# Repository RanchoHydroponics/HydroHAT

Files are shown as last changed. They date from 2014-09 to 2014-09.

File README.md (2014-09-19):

HydroHAT
========

The HydroHAT is an Arduino-based extension to the RPi Model B+. It controls sensors and actuators over I2C and takes care of control loops and lower-level logic, while using the RPi to run the user interface, via a touchscreen and a web interface.

In our case, it is being developed and used to control a hydroponics system, however, it should function well as a general controller for automation via RPi.

Additionally, the UART TX and RX from the RPi are passed through to a 4D Systems header for use with a 4D Systems touchscreen.

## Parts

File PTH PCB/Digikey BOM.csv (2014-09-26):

Digikey PN | Qty
478-5741-ND | 4
ATMEGA1284P-PU-ND | 1
768-1007-1-ND | 1
CAT24C32LI-G-ND | 1
952-1767-ND | 1
952-2219-ND | 1
A19470-ND | 2
609-3221-ND | 1
A19471-ND | 1
A1922-ND | 1
CF14JT10K0CT-ND | 1
490-1215-ND | 1
450-1650-ND | 1
296-16843-1-ND | 3

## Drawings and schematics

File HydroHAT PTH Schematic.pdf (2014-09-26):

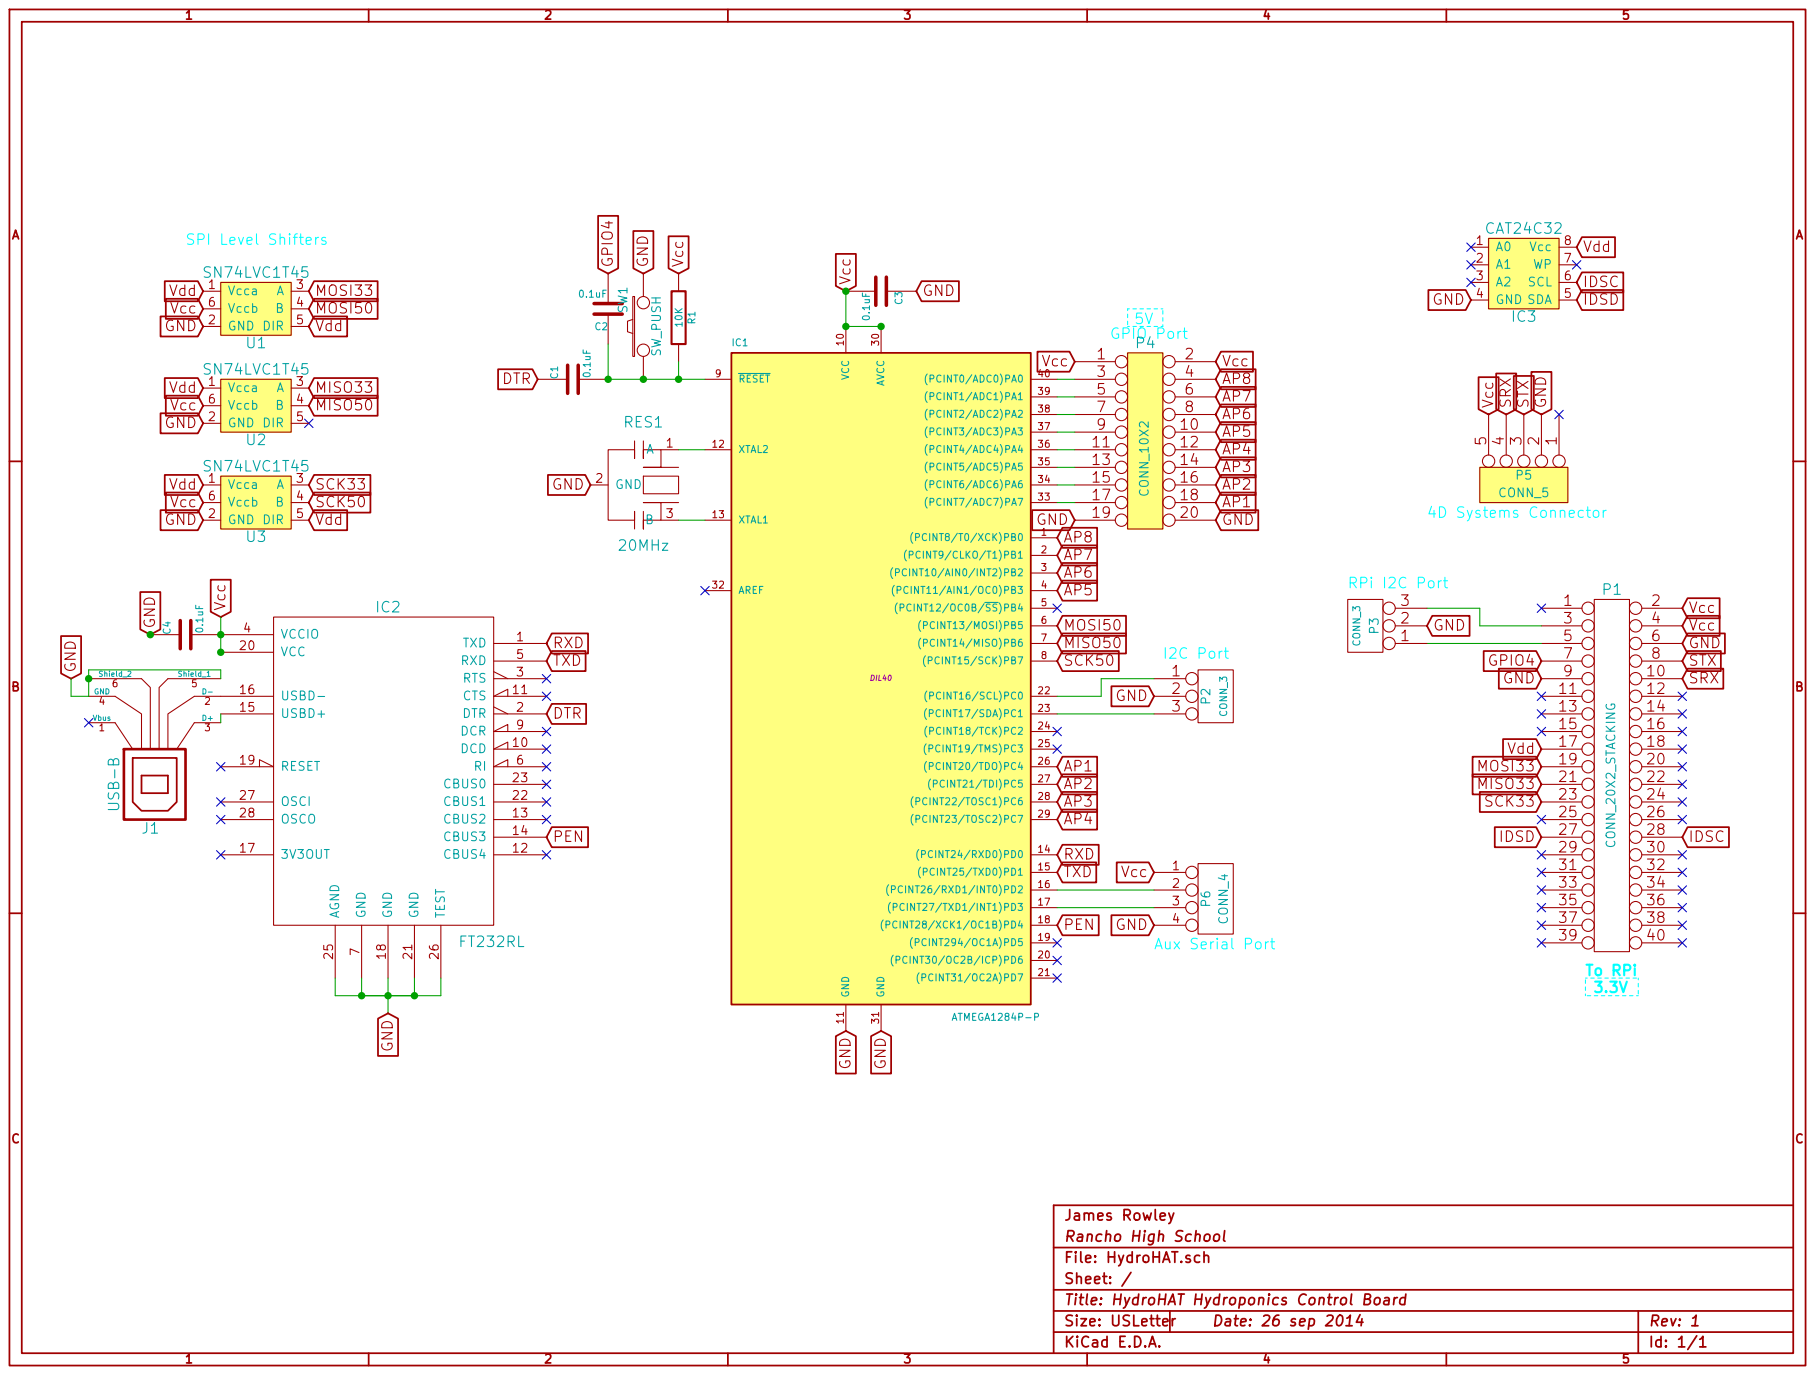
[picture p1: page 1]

SCK50 Vdd Vdd Vdd Vdd Vcc Vcc Vcc GND

P5 CONN_5 Vcc SRX STX GND

7 DCR 9 DCD 10 VCC 20 CTS 11 GND 21 CBUS4 12 CBUS1 22 CBUS2 13 CBUS0 23 CBUS3 14 USBD+ 15 AGND 25 USBD- 16 TEST 26

James Rowley
Rancho High School
File: HydroHAT.sch
Sheet: /
Title: HydroHAT Hydroponics Control Board
KiCad E.D.A.

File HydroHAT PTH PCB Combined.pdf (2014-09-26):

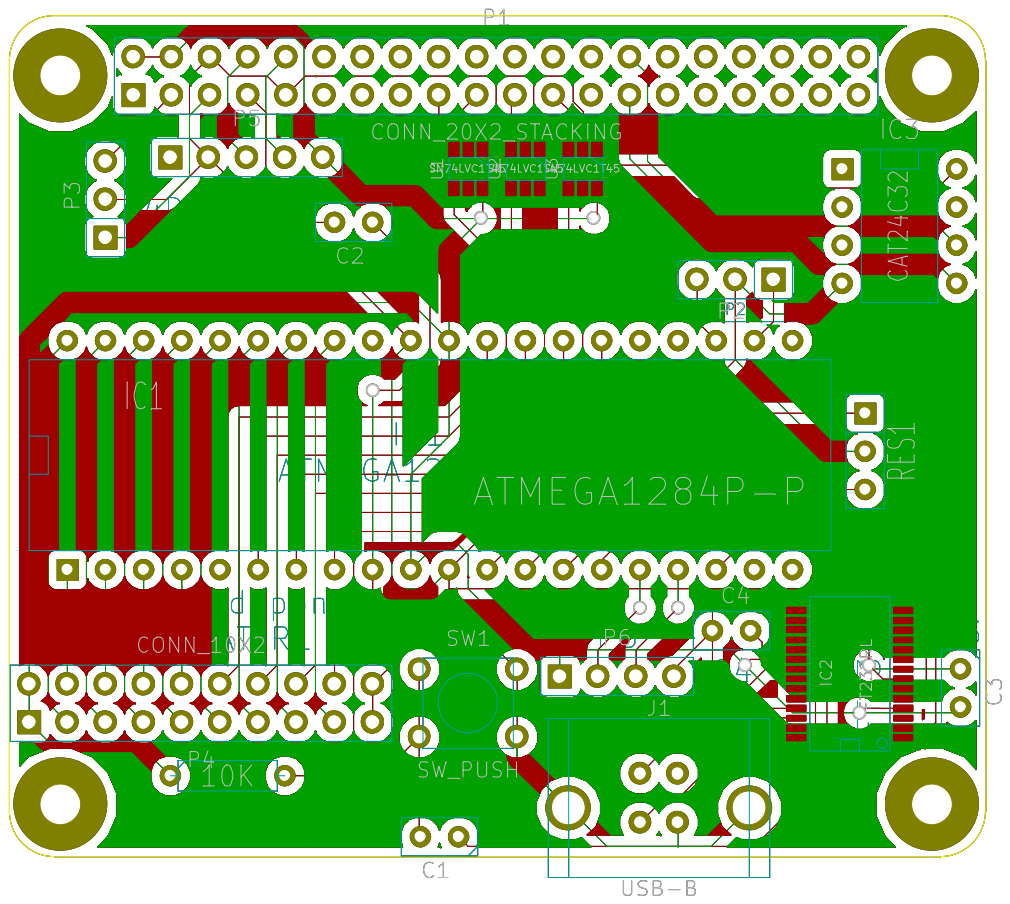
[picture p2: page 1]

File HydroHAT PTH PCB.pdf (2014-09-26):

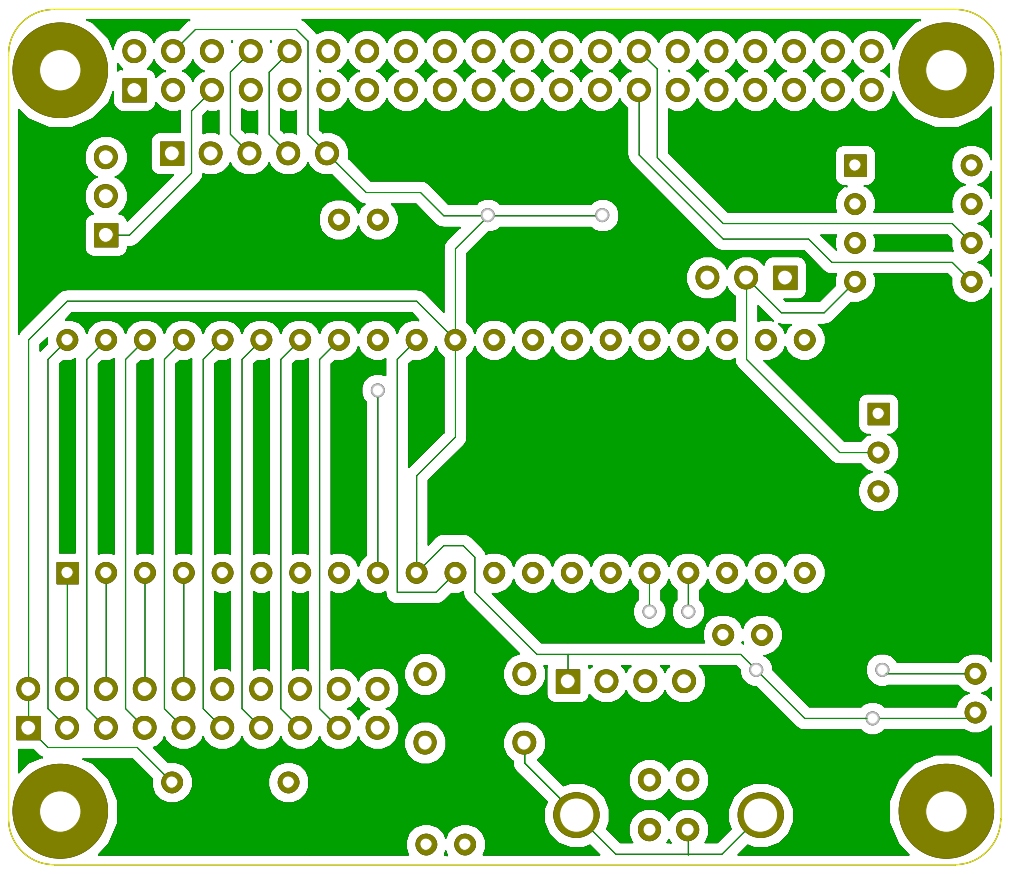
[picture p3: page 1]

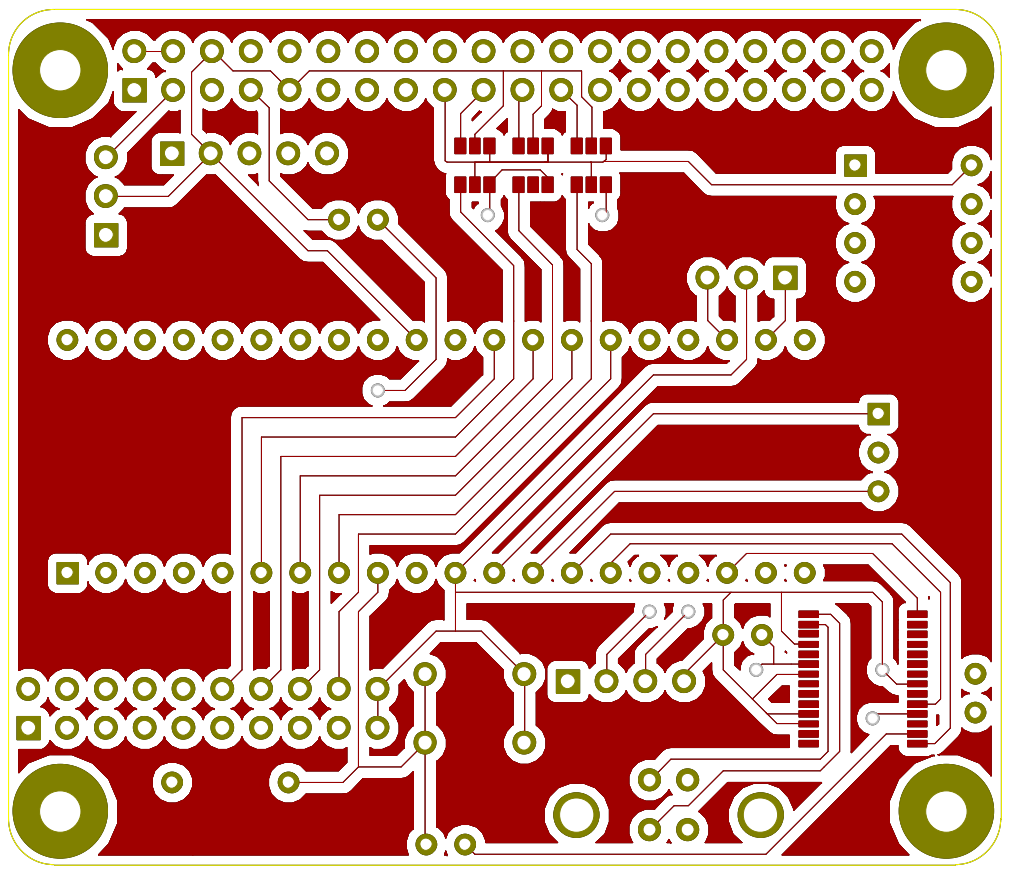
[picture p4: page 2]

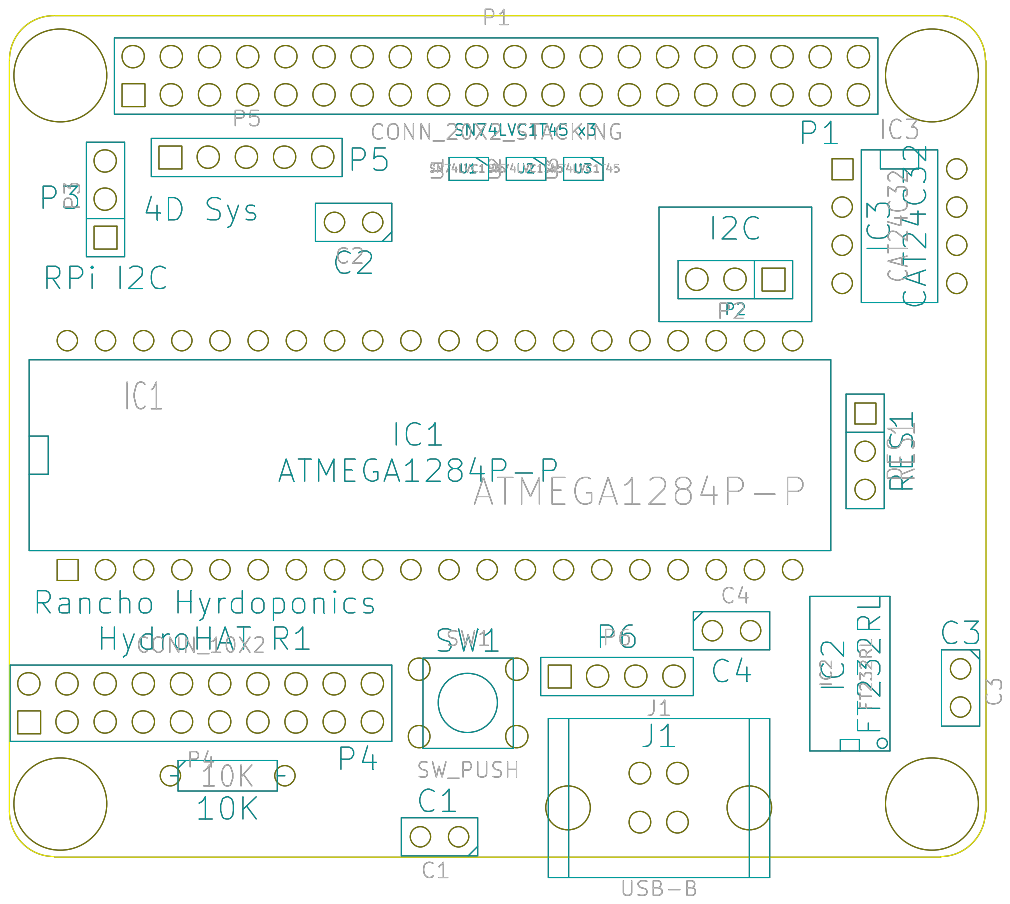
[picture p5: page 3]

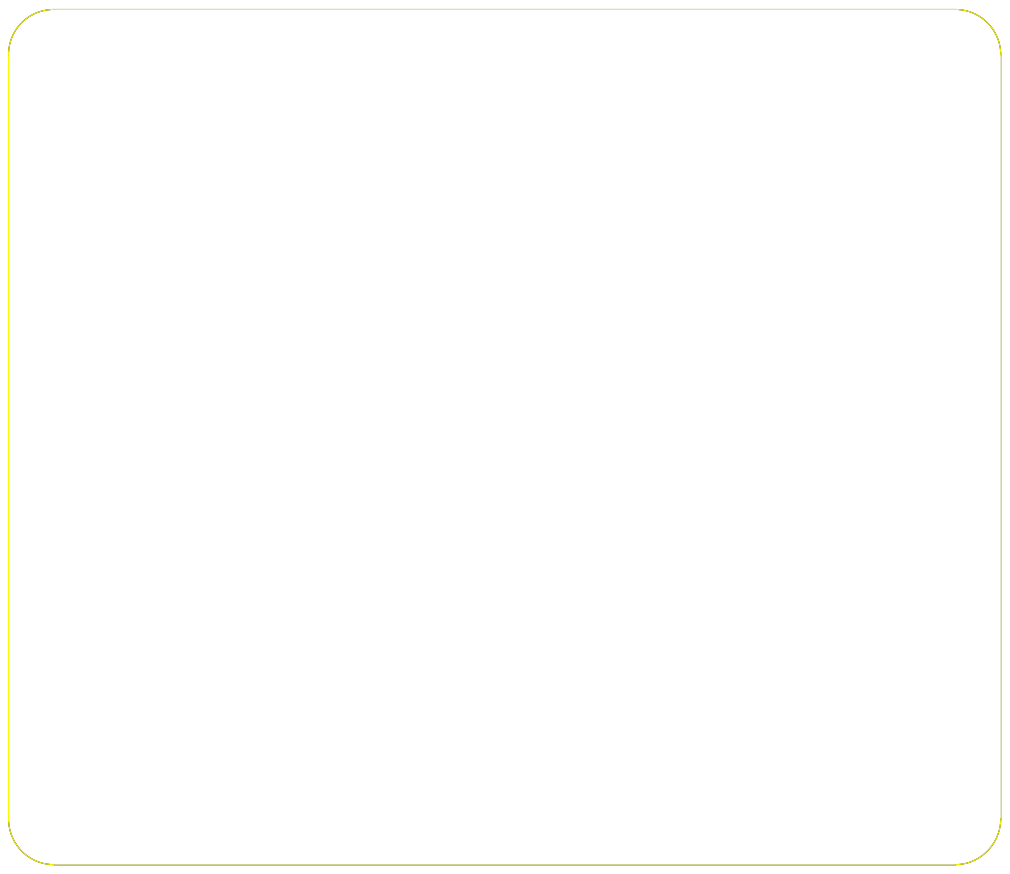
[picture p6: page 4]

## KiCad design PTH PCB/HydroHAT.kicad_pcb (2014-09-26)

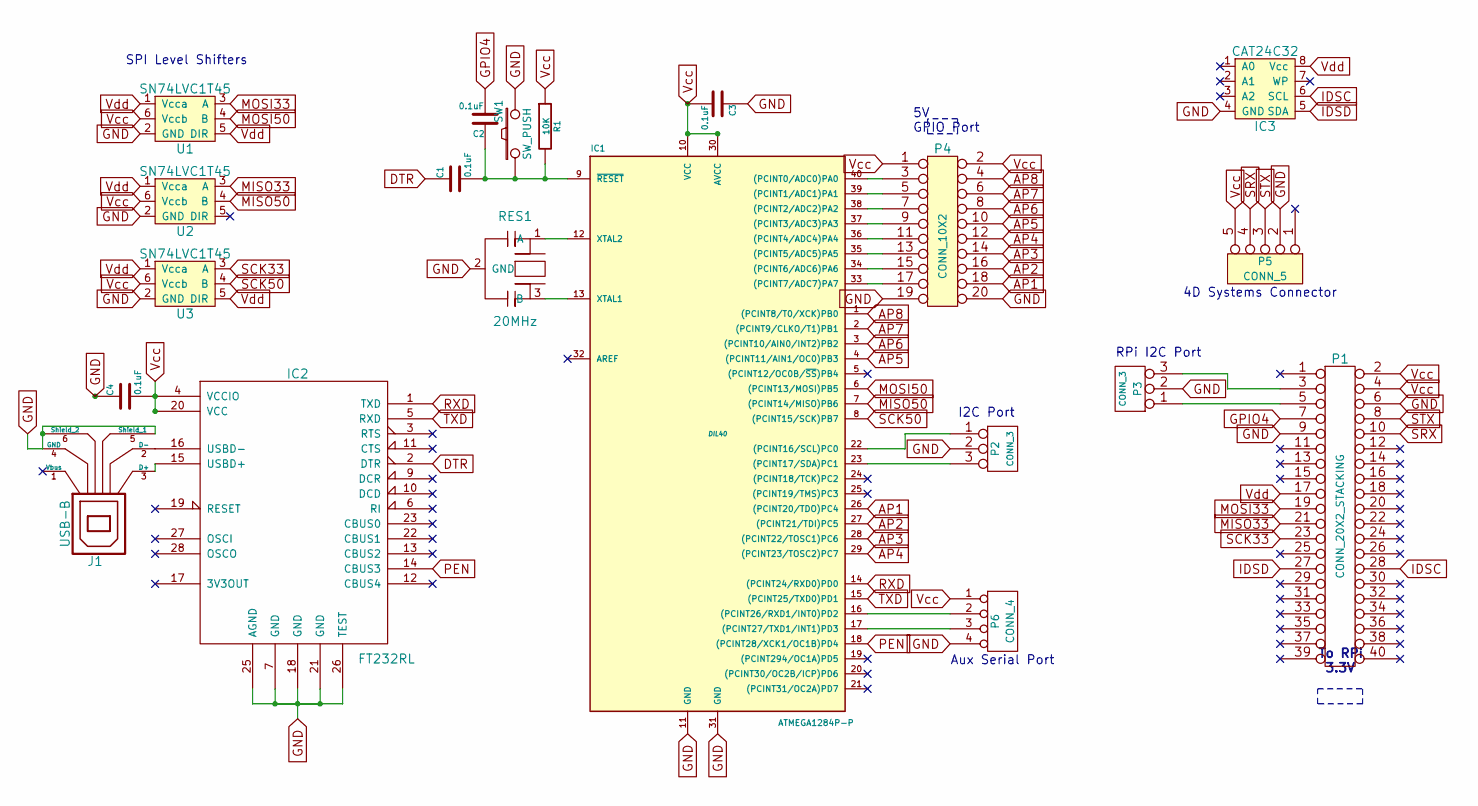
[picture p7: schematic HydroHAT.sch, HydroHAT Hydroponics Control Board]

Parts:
C1, C2, C3, C4: 0.1uF; MFG Part Num SR295E104MAR
IC1: ATMEGA1284P-P; DIL40; MFG Part Num ATMEGA1284P-PU
IC2: FT232RL; MFG Part Num FT232RL-TUBE
IC3: CAT24C32; MFG Part Num CAT24C32LI-G
J1: USB-B; MFG Part Num M701-330442
P1: CONN_20X2_STACKING; MFG Part Num M20-6102045
P2, P3: CONN_3; MFG Part Num 640456-3
P4: CONN_10X2; MFG Part Num 67996-420HLF
P5: CONN_5; MFG Part Num 640456-5
P6: CONN_4; MFG Part Num 640456-4
R1: 10K; MFG Part Num CF14JT10K0
RES1: 20MHz; MFG Part Num CSTLS20M0X53-B0
SW1: SW_PUSH; MFG Part Num 1825910-6
U1, U2, U3: SN74LVC1T45; MFG Part Num SN74LVC1T45DBVR

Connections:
AP1: IC1.26 ((PCINT20/TDO)PC4), P4.18
AP2: IC1.27 ((PCINT21/TDI)PC5), P4.16
AP3: IC1.28 ((PCINT22/TOSC1)PC6), P4.14
AP4: IC1.29 ((PCINT23/TOSC2)PC7), P4.12
AP5: IC1.4 ((PCINT11/AIN1/OC0)PB3), P4.10
AP6: IC1.3 ((PCINT10/AIN0/INT2)PB2), P4.8
AP7: IC1.2 ((PCINT9/CLKO/T1)PB1), P4.6
AP8: IC1.1 ((PCINT8/T0/XCK)PB0), P4.4
DTR: C1.1, IC2.2 (DTR)
GND: C3.1, C4.1, IC1.11 (GND), IC1.31 (GND), IC2.7 (GND), IC2.18 (GND), IC2.21 (GND), IC2.25 (AGND), IC2.26 (TEST), IC3.4 (GND), J1.4 (GND), J1.5 (Shield_1), J1.6 (Shield_2), P1.6, P1.9, P2.2 (PM), P3.2 (PM), P4.19, P4.20, P5.2, P6.4, RES1.2 (GND), SW1.2, U1.2 (GND), U2.2 (GND), U3.2 (GND)
GPIO4: C2.2, P1.7
IDSC: IC3.6 (SCL), P1.28
IDSD: IC3.5 (SDA), P1.27
MISO33: P1.21, U2.3 (A)
MISO50: IC1.7 ((PCINT14/MISO)PB6), U2.4 (B)
MOSI33: P1.19, U1.3 (A)
MOSI50: IC1.6 ((PCINT13/MOSI)PB5), U1.4 (B)
unnamed: P1.5, P3.1
unnamed: IC1.23 ((PCINT17/SDA)PC1), P2.3
unnamed: IC1.17 ((PCINT27/TXD1/INT1)PD3), P6.3
unnamed: IC1.16 ((PCINT26/RXD1/INT0)PD2), P6.2
unnamed: IC1.13 (XTAL1), RES1.3 (B)
unnamed: IC1.12 (XTAL2), RES1.1 (A)
unnamed: IC1.33 ((PCINT7/ADC7)PA7), P4.17
unnamed: IC2.15 (USBD+), J1.3 (D+)
unnamed: IC2.16 (USBD-), J1.2 (D-)
unnamed: IC1.22 ((PCINT16/SCL)PC0), P2.1
unnamed: P1.3, P3.3
unnamed: IC1.40 ((PCINT0/ADC0)PA0), P4.3
unnamed: IC1.39 ((PCINT1/ADC1)PA1), P4.5
unnamed: IC1.38 ((PCINT2/ADC2)PA2), P4.7
unnamed: IC1.37 ((PCINT3/ADC3)PA3), P4.9
unnamed: IC1.36 ((PCINT4/ADC4)PA4), P4.11
unnamed: IC1.35 ((PCINT5/ADC5)PA5), P4.13
unnamed: IC1.34 ((PCINT6/ADC6)PA6), P4.15
unnamed: C1.2, C2.1, IC1.9 (~RESET), R1.2, SW1.1
PEN: IC1.18 ((PCINT28/XCK1/OC1B)PD4), IC2.14 (CBUS3)
RXD: IC1.14 ((PCINT24/RXD0)PD0), IC2.1 (TXD)
SCK33: P1.23, U3.3 (A)
SCK50: IC1.8 ((PCINT15/SCK)PB7), U3.4 (B)
SRX: P1.10, P5.4
STX: P1.8, P5.3
TXD: IC1.15 ((PCINT25/TXD0)PD1), IC2.5 (RXD)
Vcc: C3.2, C4.2, IC1.10 (VCC), IC1.30 (AVCC), IC2.4 (VCCIO), IC2.20 (VCC), P1.2, P1.4, P4.1, P4.2, P5.5, P6.1, R1.1, U1.6 (Vccb), U2.6 (Vccb), U3.6 (Vccb)
Vdd: IC3.8 (Vcc), P1.17, U1.1 (Vcca), U1.5 (DIR), U2.1 (Vcca), U3.1 (Vcca), U3.5 (DIR)

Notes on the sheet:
To RPi 3.3V
Aux Serial Port
5V GPIO Port
I2C Port
RPi I2C Port
SPI Level Shifters
4D Systems Connector

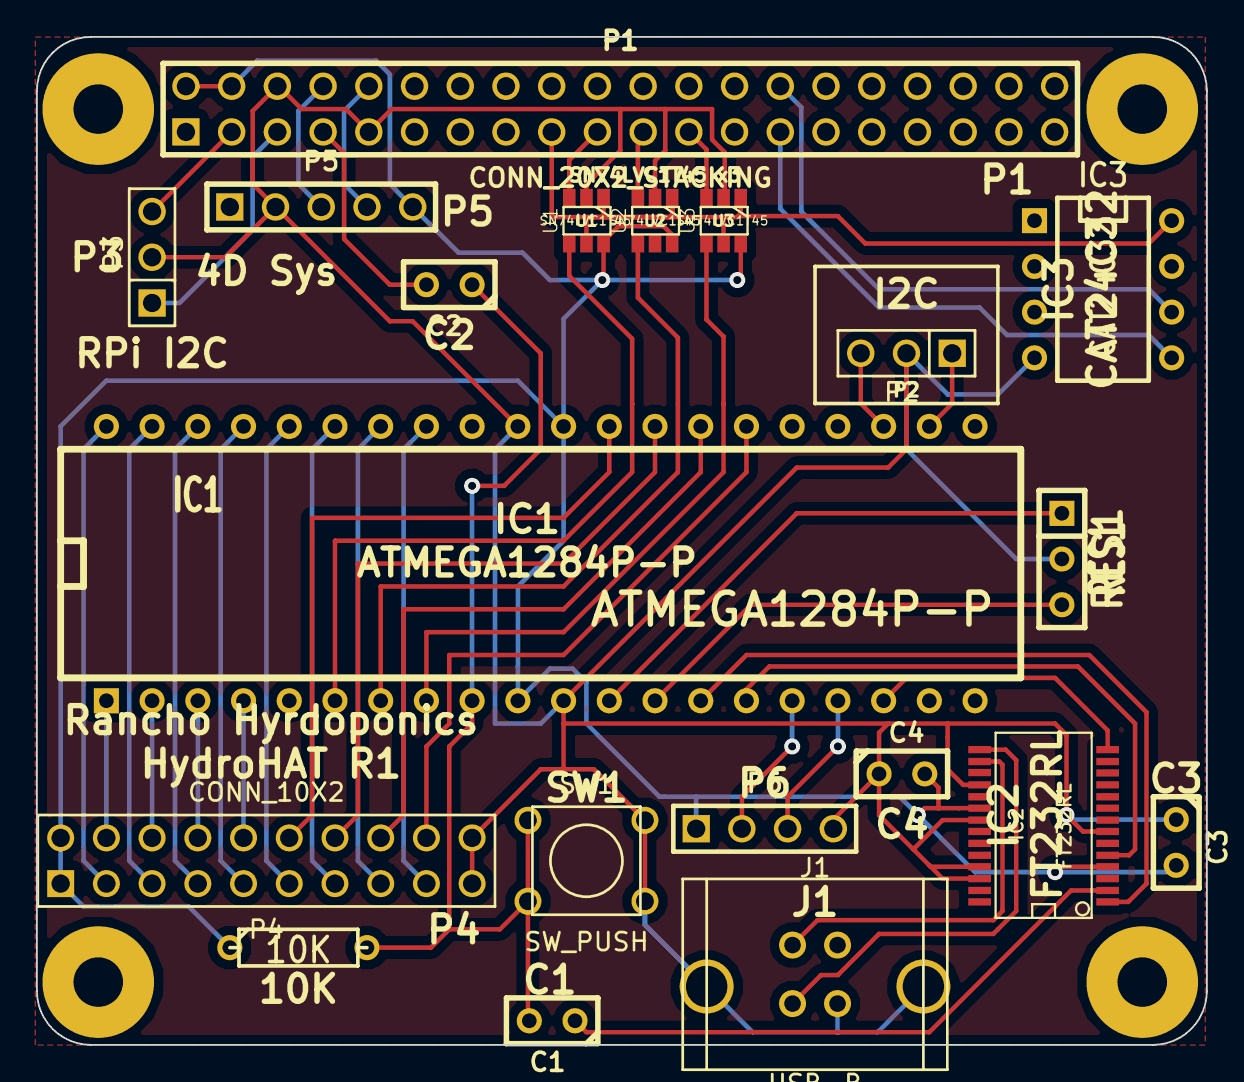
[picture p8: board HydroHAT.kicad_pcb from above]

Board: 2 copper layers, 65.0 x 56.0 mm, 24 parts (0 on the bottom side), 45 nets.

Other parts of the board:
HAT-Hole: VAL**; HAT-Hole
HAT-Hole#2, HAT-Hole#3, HAT-Hole#4: VAL**; HAT-Hole

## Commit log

2014-09-19 Updated Readme
    And added KiCad project
2014-09-22 PCB Edges
    [HydroHAT.kicad_pcb]
2014-09-23 Schematic start
    And mostly done, still need to add FTDI
    [HydroHAT.kicad_pcb, HydroHAT.sch]
2014-09-23 Changed Things
    Stuff
    [HydroHAT.sch]
2014-09-23 Added level shifting to schematic
    [HydroHAT.sch]
2014-09-23 Started USB circuitry
    [HydroHAT.sch]
2014-09-24 Almost done
    Just need to add two datasheets
    [HydroHAT.sch]
2014-09-25 Schematic Done
    Working on footprints
    [HydroHAT.kicad_pcb, HydroHAT.sch]
2014-09-26 PTH PCB Complete
    Schematic also somewhat reworked.
    [HydroHAT.kicad_pcb, HydroHAT.sch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]
2014-09-26 Updated Schematic PDF
    Whoops
2014-09-26 Added BOM And rejiggled some stuff
    [Digikey BOM.csv, Digikey BOM.xls, HydroHAT.csv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]
2014-10-11 Added stencil stuff
    Yep
    [HydroHAT-F_Paste.gtp]
